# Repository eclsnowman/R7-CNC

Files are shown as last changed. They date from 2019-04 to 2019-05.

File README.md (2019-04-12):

# R7-CNC BY SMW3D AKA Hobby-Fab (w/ Eric Lien)
=========

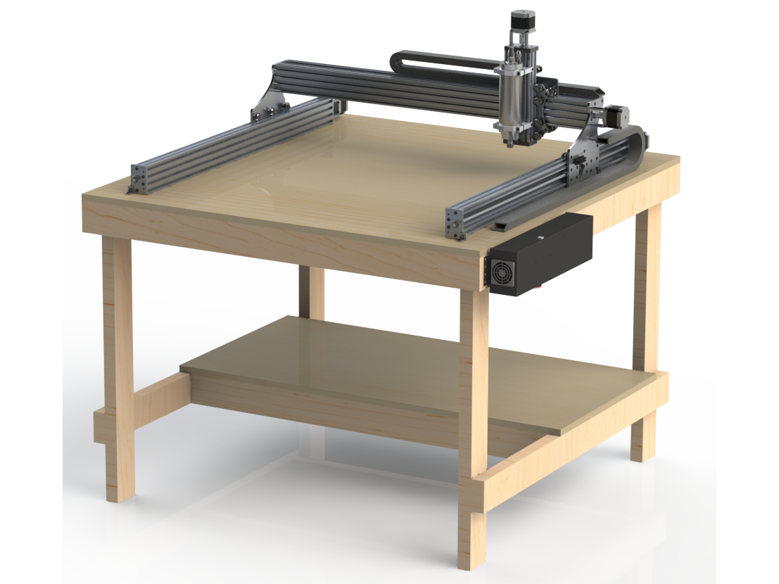
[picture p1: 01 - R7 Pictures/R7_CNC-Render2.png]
R7-CNC Render Image2


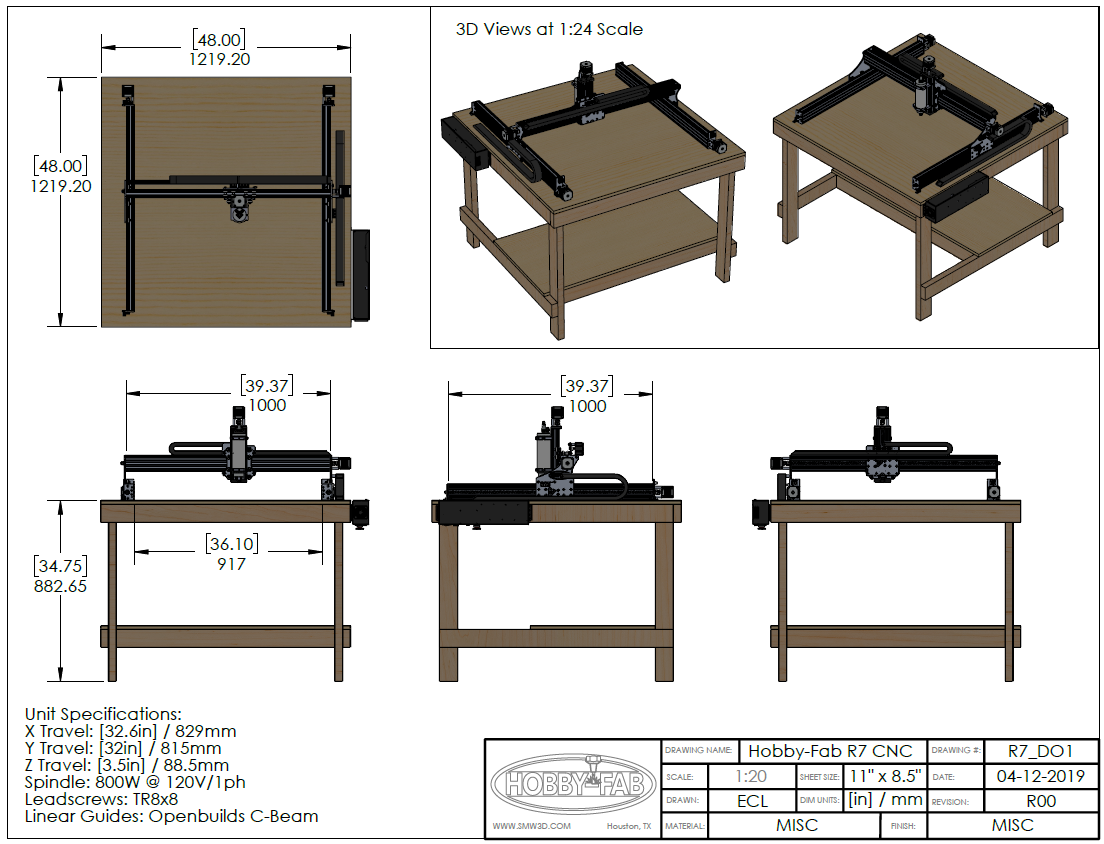
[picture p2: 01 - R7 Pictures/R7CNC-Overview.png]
R7-CNC Overview


The R7-CNC is a strong and capable router style CNC that was sold by SMW3D which later changed its name to Hobby-Fab. I have had the pleasure of knowing Brandon Satterfield for many years through the now defunct Google+. Over those years I have had the pleasure of working on many cool project with Brandon and the team at SMW3D. The R7 CNC was one of those projects. 

Unfortunately the Chinese market spurring the race to the bottom on maker parts, kits, and components drove Brandon and his team on to greener pastures via the closure of Hobbyfab in 2019. But I am delighted to announce that Brandon has given me the OK to release the designs and plans on many of the cool machines we developed together out here on Github. After the initial designs we worked on together several years ago, Brandon and his team made many improvements and upgrades to those initial designs. There is no better example of that than the R7-CNC which was subject to continuous improvement. The files here are my best attempt to cleanup and document via detailed 3D models the final product as shipped by Hobbyfab.

In this Github you will find a detailed 3D model generated by me for the mechanical setup of the machine. I have the files saved in several formats. I work in solidworks natively, but I have exported the model into Fusion360, X_T, Step, 3D-PDF. In addition I have generated a DXF for the plates that make up the major fabricated components.

In addition to the models, I have included several of the supporting files Brandon had developed for his product, like manuals, reference material, etc. Some of this material might be slightly outdated to the model. But it should aid in helping a perspective maker in replicating this capable CNC router design on their own.

I would like to end this by saying Brandon and his group over the years they were in business did amazing work for the community. They sponsored projects to many makers via at cost or free components to develop cool projects. They were always available to answer questions to potential makers on the kits and projects they sold (day or night). The maker community lost something special with the closure of SMW3D/Hobby-Fab. But the impact they left on the maker community will live on.

Thank you Brandon and team. You are amazing. And I am glad to have been but a small part in your chapter of the Maker Revolution story.

-Eric Lien

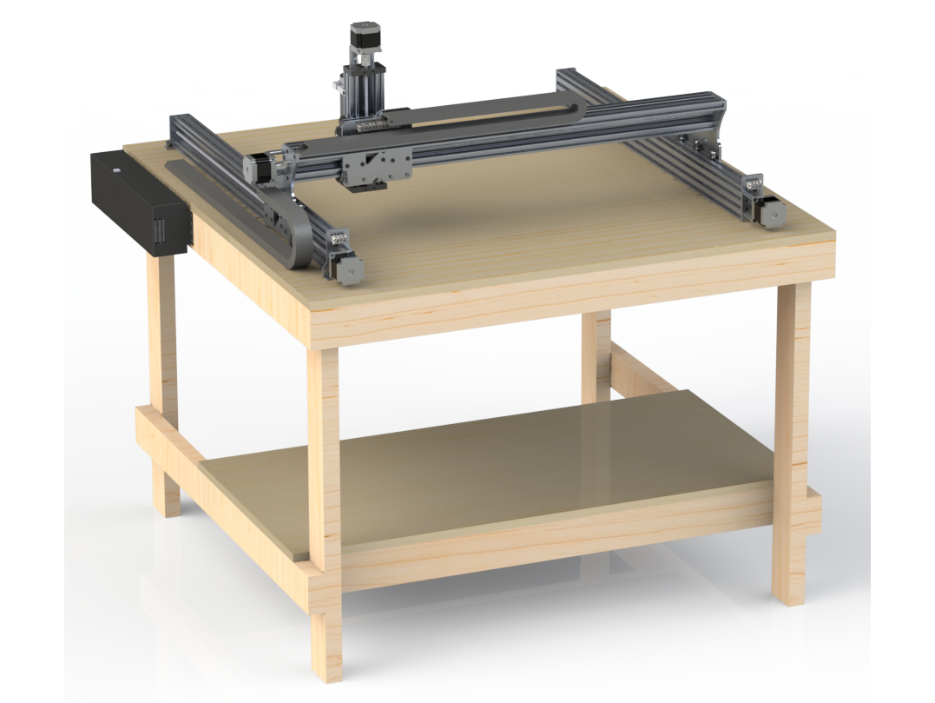
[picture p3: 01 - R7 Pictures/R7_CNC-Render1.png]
R7-CNC Render Image1


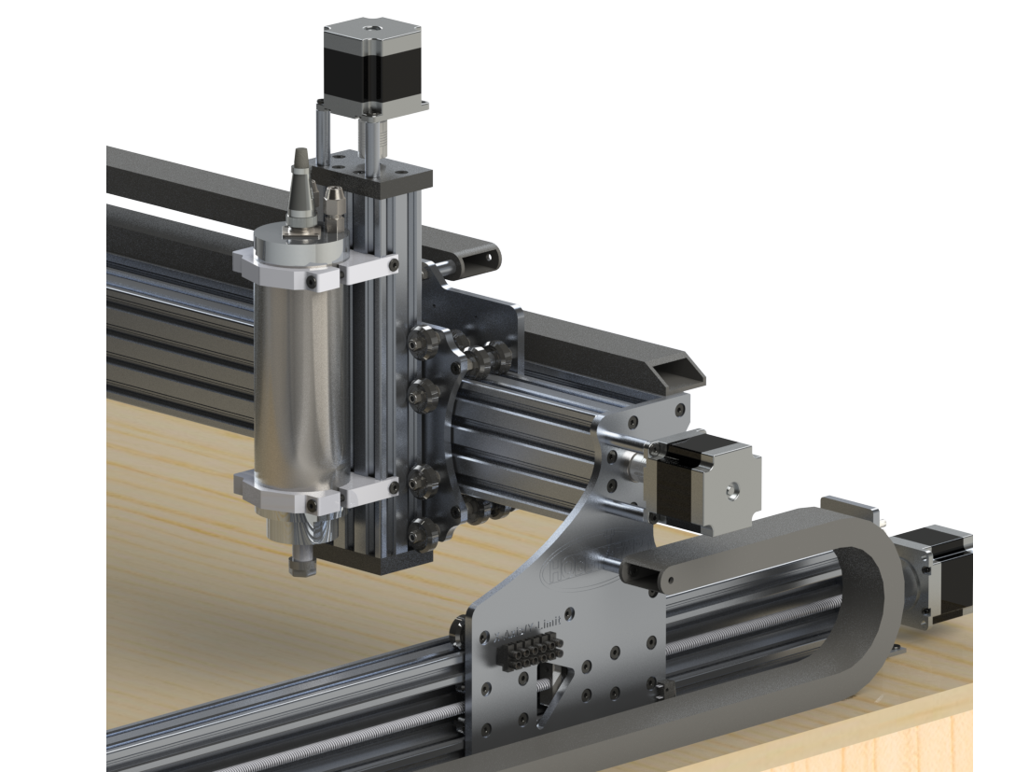
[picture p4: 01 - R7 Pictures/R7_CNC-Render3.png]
R7-CNC Render Image3


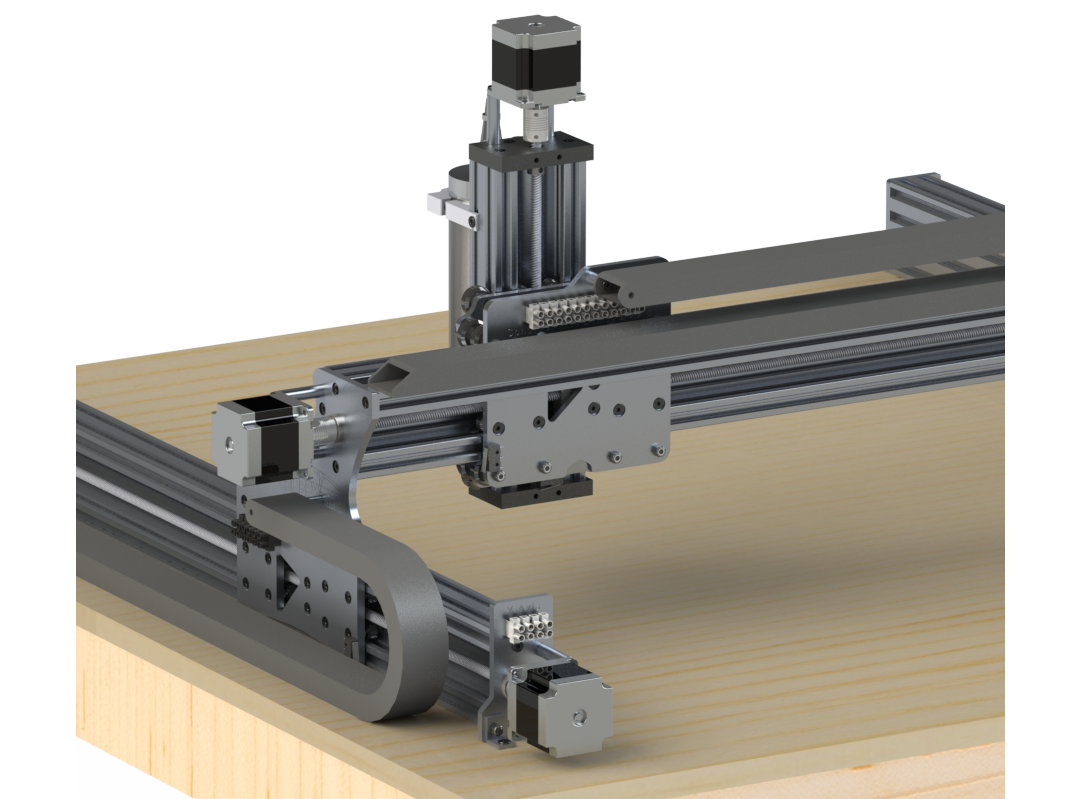
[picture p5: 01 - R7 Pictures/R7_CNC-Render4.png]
R7-CNC Render Image4


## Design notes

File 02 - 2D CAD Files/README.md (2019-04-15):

# Image of DXF 2D Print
=========

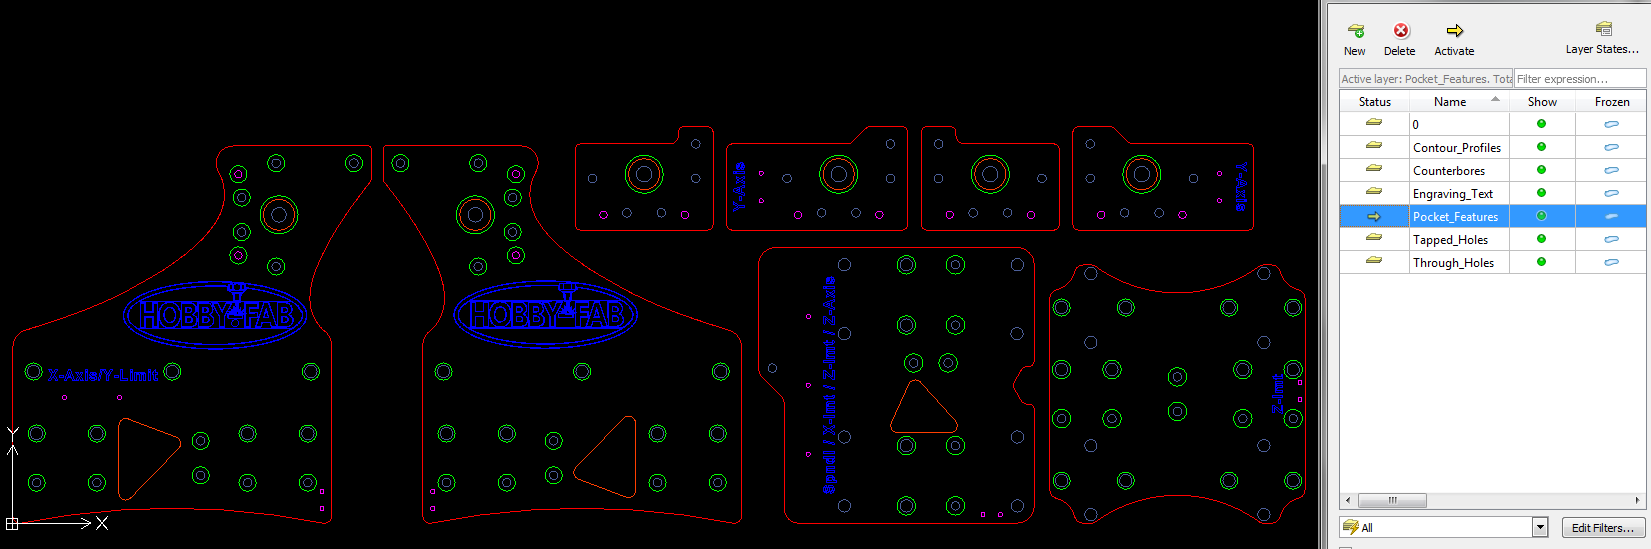
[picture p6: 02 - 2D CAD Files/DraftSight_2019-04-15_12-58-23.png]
Image of DXF


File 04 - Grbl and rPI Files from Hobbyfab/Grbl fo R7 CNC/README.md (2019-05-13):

Grbl files for Hobbyfab R7 CNC, Files based on Spindle Size (example 800W)

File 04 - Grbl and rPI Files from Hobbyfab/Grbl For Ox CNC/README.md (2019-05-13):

Grbl files for Hobbyfab Ox, Files based on Spindle Size (400W vs 600W)

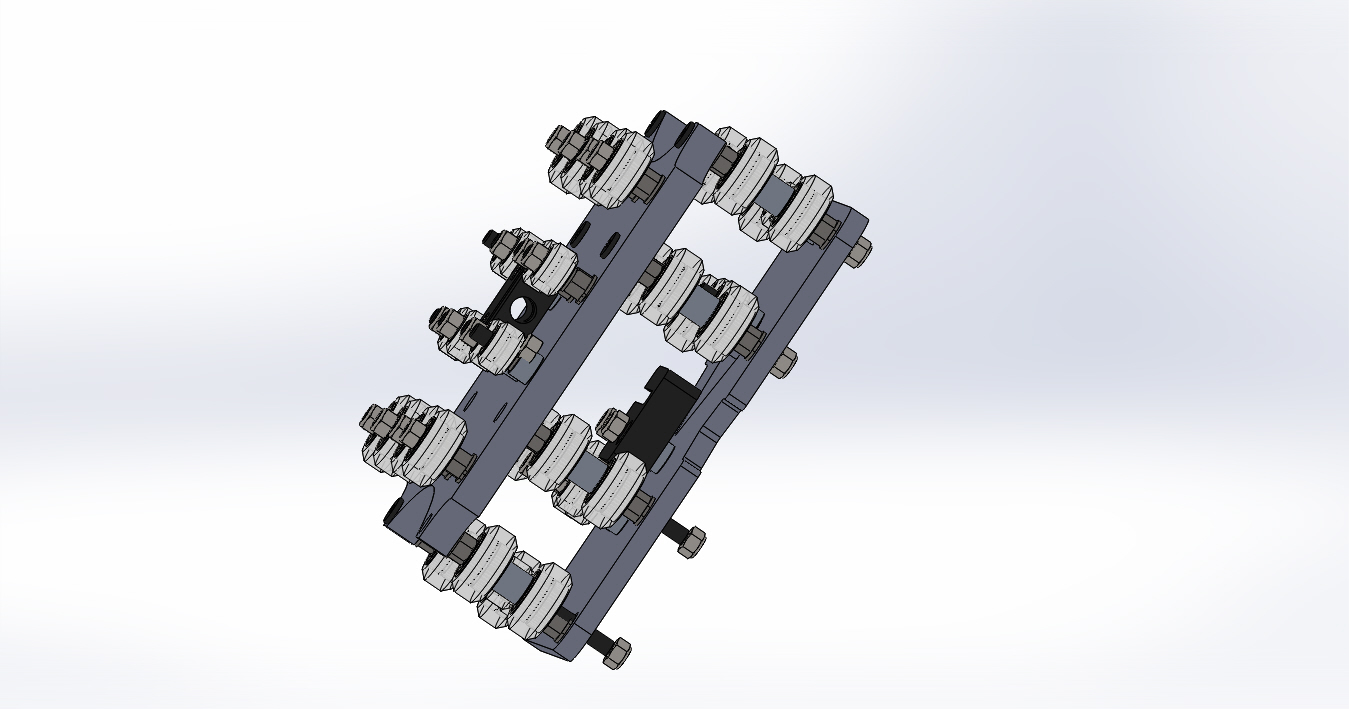
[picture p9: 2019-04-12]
00 - R7 Documentation/Images/X_Z gantry2.JPG

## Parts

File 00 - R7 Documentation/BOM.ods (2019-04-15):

STEP 1 | Qty. | Cost Per Unit | Price
Y Gantry Plate LH | 1
Y Gantry Plate RH | 1
Xtreme Wheels | 6 | $6.75 | $40.50
Mini Xtreme Wheels | 16 | $5.95 | $95.20
Anti-BackLash Acme block | 2 | $9.85 | $19.70
6mm Spacers | 8 | $0.20 | $1.60
6mm Mini Eccentric Spacers | 14 | $2.00 | $28.00
3mm Spacers | 4 | $0.20 | $0.80
M5x20 | 4 | $0.19 | $0.76
M5x25 | 22 | $0.20 | $4.40
 |  | Total | $190.96
STEP 2 | Qty. | Cost Per Unit | Price
Front XZ Gantry Plate | 1 |  | 0
Xtreme Wheels | 8 | $6.75 | $54.00
Mini Xtreme Wheels | 8 | $5.95 | $47.60
Acme Blocks | 2 | $9.85 | $19.70
6mm Spacers | 4 | $0.20 | $0.80
6mm Mini Eccentric Spacers | 12 | $2 | $24
3mm Spacers | 4 | $0.20 | $0.80
M5x20 | 4 | $0.19 | $0.76
M5x25 | 16 | $0.20 | $3.20
250mm ACME | 1 | $9.99 | $9.99
M5 Nuts | 4 | 0.12 | 0.48
 |  | Total | $161.33
STEP 3 | Qty. | Cost Per Unit | Price
Rear XZ Gantry Plate | 1 |  | 0
Anti-BackLash Acme Block | 1 | $9.85 | $9.85
Mini Xtreme Wheels | 8 | $5.95 | $47.60
3mm spacers | 2 | $0.20 | $0.40
m5x20 | 2 | $0.19 | $0.38
m5x25 | 8 | $0.20 | $1.60
6mm Spacers | 4 | $0.20 | $0.80
Eccentric | 4 | $2 | $8
M5 Nuts | 2 | 0.12 | 0.24
 |  | Total | $68.87
STEP 4 | Qty. | Cost Per Unit | Price
Xtreme Wheels | 16 | $6.75 | $108
9mm Spacers | 8 | $0.20 | $2
6mm Mini Eccentric Spacers | 16 | $2.00 | $32
M5x60 | 8 | $0.30 | $2
 |  | Total | $144.00
STEP 5 | Qty. | Cost Per Unit | Price
800w Spindle | 1 | $160 | $160
Spindle Clamps | 2 | 1.25 | $3
Solid black 90s | 8 | $2.25 | $18
M5 T-Nuts | 8 | $0.20 | $2
M5x8 | 8 | $0.18 | $1
M5x10 | 8 | $0.18 | $1
M5x40 | 2 | $0.25 | $1
250mm C-Beam | 1 | 7 | $7
 |  | Total | $192.48
STEP 6 | Qty. | Cost Per Unit | Price
M5x15 | 10 | $0.19 | $1.90
M5x55 | 2 | $0.30 | $0.60
1.5in spacers | 2 | $0.75 | $1.50
608ZZ | 2 | $6.15 | $12.30
lock collar | 1 | $1.20 | $1.20
6.35x8 Coupler | 1 | $1.50 | $1.50
1000mm Acme | 1 | $31.50 | $31.50
1000mm 20x20 | 1 | $10 | $10.00
1000mm C Beam | 1 | $28 | $28.00
NEMA 23 2.8A | 1 | $23.99 | $23.99
 |  | Total | $112.49
Step 7 | Qty. | Cost Per Unit | Price
NEMA 23 2.8A | 2 | $23.99 | $47.98
6.35x8 Coupler | 2 | $1.50 | $3.00
End corner caps | 4 | 10 | $40.00
Lock collar | 2 | $1.20 | $2.40
608ZZ | 4 | $6.15 | $24.60
C-Beam 1000mm | 2 | $28.00 | $56.00
1.5" spacers | 4 | $0.75 | $3.00
M5x55mm bolts | 4 | $0.30 | $1.20
M5x20mm bolts | 20 | $0.19 | $3.80
Single corner bracket | 4 | 1 | $4.00
M5 nuts | 4 | $0.12 | $0.48
1000mm ACME | 2 | $31.50 | $63.00
ACME flange nut | 1 | 6.25 | $6.25
 |  | Total | $255.71
Step 8 | Qty. | Cost Per Unit | Price
C-beam end plates | 2 | $8.75 | $17.50
M5x55 | 2 | $0.30 | $0.60
1.5" spacers | 2 | $0.75 | $1.50
250mm ACME | 1 | $9.99 | $9.99
688zz | 2 | $0.99 | $1.98
6.35mm x 8mm coupler | 1 | $1.50 | $1.50
NEMA 23 2.8A | 1 | $23.99 | $23.99
M5x25mm | 8 | $0.19 | $1.52
Lock Collar | 2 | $1.20 | $2.40
 |  | Total | $60.98
Step 9 | Qty. | Cost Per Unit | Price
3/16" ID 5/16" OD vinyl tubing | 30 | 1.08 | 32.4
4 wire 22g | 30 | $0.50 | $15.00
16-3 wire | 15 | 0.5 | 7.5
15mmx30mm cable chain | 2 | $16.00 | $32.00
M5 drop-in T-nut | 1 | $0.75 | $0.75
M5 x 10mm bolt | 1 | $0.18 | $0.18
small heat shrink tubing | 4 | $1.25 | $5.00
M5x65mm bolt | 1 | $0.30 | $0.30
40mm spacer | 1 | $0.20 | $0.20
9mm spacer | 1 | $0.20 | $0.20
6mm spacer | 2 | $0.20 | $0.40
Water pump | 1 | $25.00 | $25.00
M5x20mm bolt | 1 | $0.19 | $0.19
Large heat shrink tubing | 4 | $1.25 | $5.00
Sheathing 10mm | 10 | $0.99 | $9.90
M5 nut | 1 | $0.12 | $0.12
Power cable | 1 | $6.50 | $6.50
 |  | Total | $140.64
Step 10 | Qty. | Cost Per Unit | Price
Fan | 1 | $4.99 | $4.99
Inverter | 1 | $150 | $150
24V power supply | 1 | $31.99 | $32.99
Power Cable | 1 | $6.50 | $6.50
 |  | Total | $194.48
 |  | Grand Total | $1,521.94

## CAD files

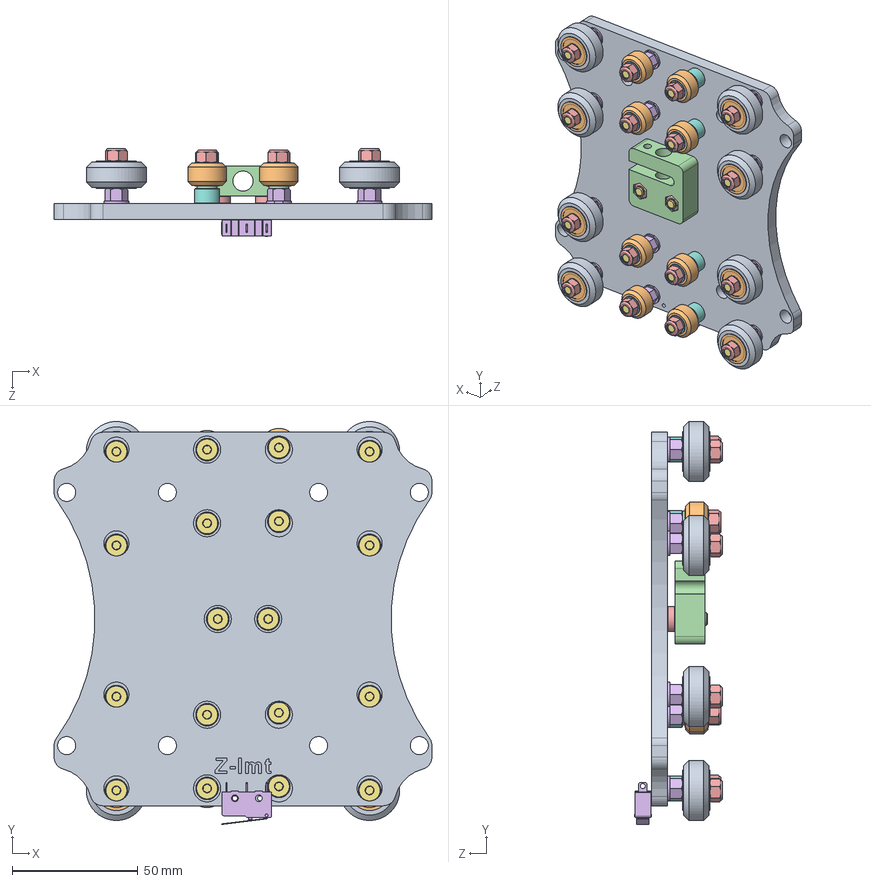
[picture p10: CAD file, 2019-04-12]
03 - 3D CAD Files/00 - Solidworks/01 - Sub Assemblies/Front XZ Gantry Plate.SLDASM
150.0 x 160.0 x 35.1 mm
R7-CNC_Plates
Xtreme Mini V Wheel x 8
Ball Bearing 5 x 10 x 4.2 x 16
Precision Shim 8 x 5 x 1 x 16
Nylon Insert Lock Nut M5 x 18
Mini Eccentric Spacer 6mm x 12
Low Profile Screw M5 x 18
Aluminum Spacer 6mm x 4
Xtreme Solid V Wheel x 8
Ball Bearing 5 x 16 x 5 x 16
Precision Shim 10 x 5 x 1 x 8
8mm Acme Anti Backlash Nut Block
Aluminum Spacer 3mm x 2
Micro Switch Button

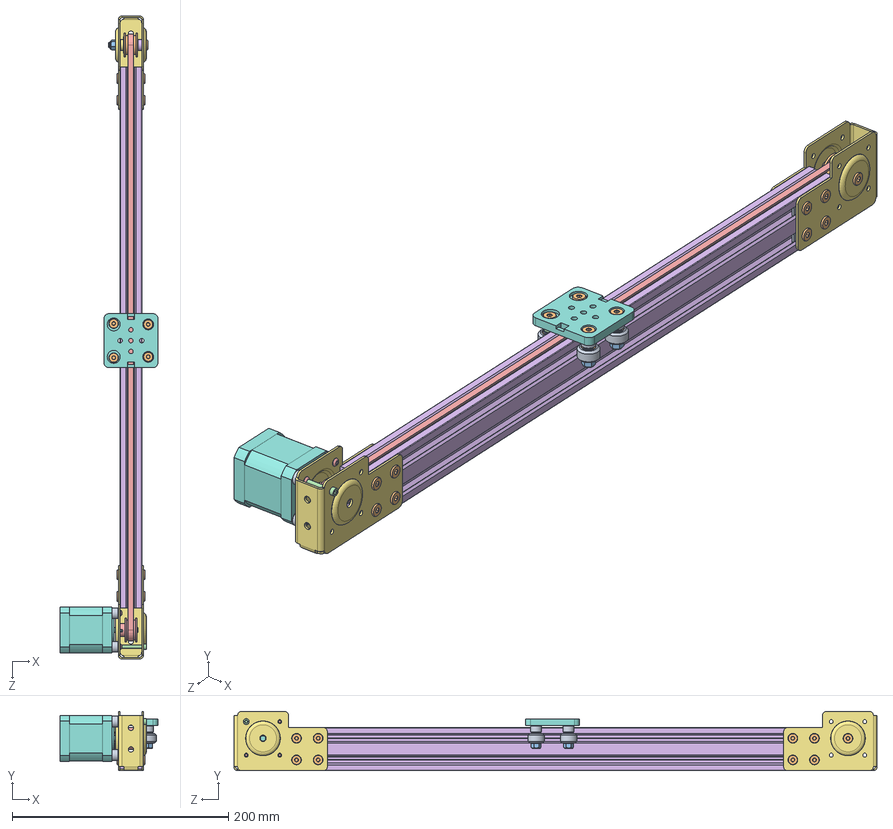
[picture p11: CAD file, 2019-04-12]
03 - 3D CAD Files/00 - Solidworks/ZZ - Openbuilds Library/Assemblies/Mini V Linear Actuator/Mini V Linear Actuator 500mm.SLDASM
90.6 x 54.9 x 594.7 mm
Double Tee Nut x 8
Low Profile Screw M5 x 21
Nylon Insert Lock Nut M5 x 5
Button Head Socket Cap Screw M3 x 4
V-Slot 20x40x500 Linear Rail
Linear Actuator End Mount x 2
Nema 17 Stepper Motor
Aluminum Spacer 6mm x 6
Smooth Idler Pulley Wheel
Ball Bearing 5 x 16 x 5 x 2
Nylon Spacer 0.125in
GT2 Timing Pulley 30 Tooth
Aluminum Spacer .25in
Aluminum Spacer .125in
Mini V Wheel Plate
Delrin Mini V Wheel x 4
Ball Bearing 5 x 10 x 4.2 x 8
Precision Shim 8 x 5 x 1 x 8
Mini Eccentric Spacer 6mm x 2
GT2 Belt 1140mm

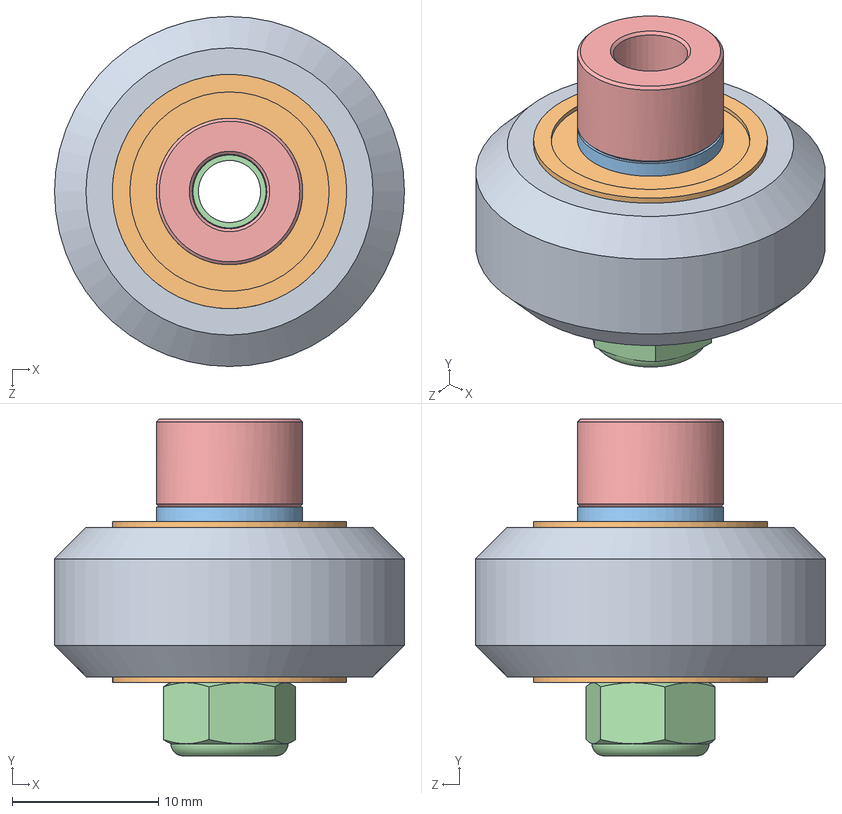
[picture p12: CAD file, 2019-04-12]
03 - 3D CAD Files/00 - Solidworks/ZZ - Openbuilds Library/Assemblies/Wheels/Solid V Wheel.SLDASM
23.9 x 23.0 x 23.9 mm
Solid V Wheel
Ball Bearing 5 x 16 x 5 x 2
Precision Shim 10 x 5 x 1 x 2
Nylon Insert Lock Nut M5
Aluminum Spacer 6mm

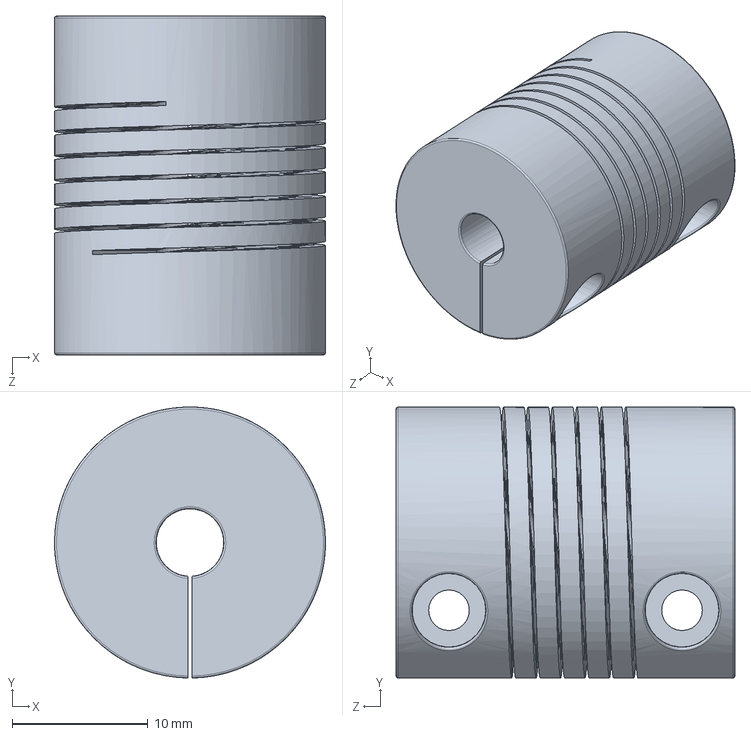
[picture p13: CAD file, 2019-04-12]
03 - 3D CAD Files/00 - Solidworks/01 - Sub Assemblies/Nema23 Drive/8mm x 6.35mm Flexible Coupling.SLDASM
20.0 x 20.0 x 25.0 mm

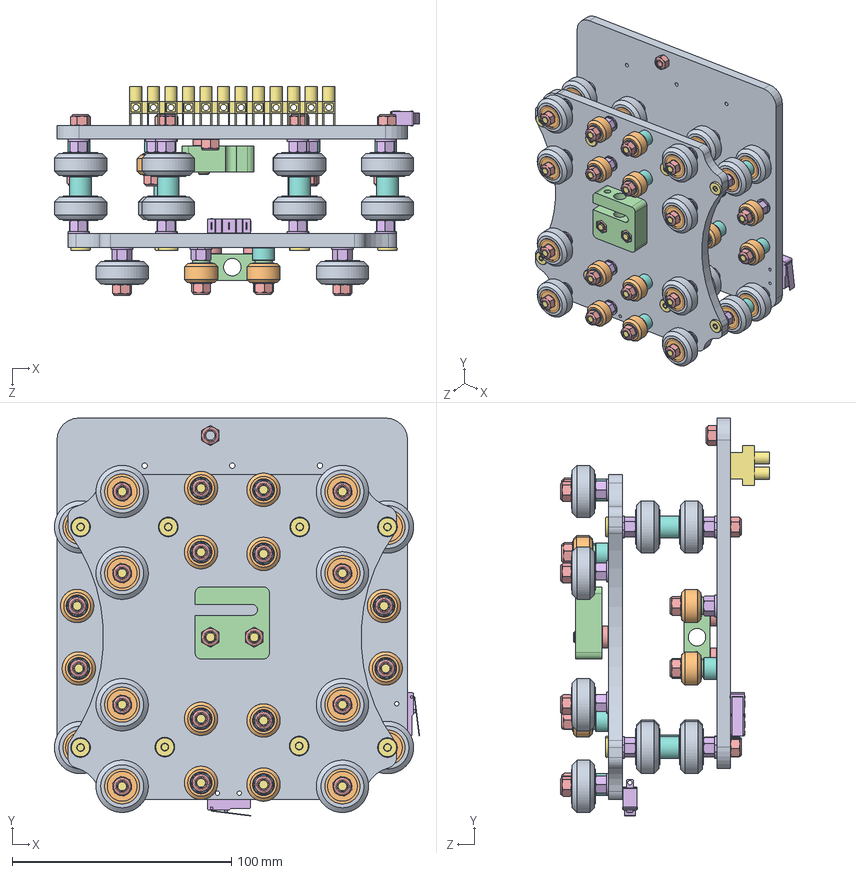
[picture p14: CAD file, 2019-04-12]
03 - 3D CAD Files/00 - Solidworks/01 - Sub Assemblies/XZ_Full_Carriage.SLDASM
166.6 x 181.6 x 95.5 mm
R7-CNC_Plates x 2
Xtreme Mini V Wheel x 16
Ball Bearing 5 x 10 x 4.2 x 32
Precision Shim 8 x 5 x 1 x 32
Nylon Insert Lock Nut M5 x 37
Mini Eccentric Spacer 6mm x 32
Low Profile Screw M5 x 36
Aluminum Spacer 6mm x 8
Xtreme Solid V Wheel x 24
Ball Bearing 5 x 16 x 5 x 48
Precision Shim 10 x 5 x 1 x 24
8mm Acme Anti Backlash Nut Block x 2
Aluminum Spacer 3mm x 4
Micro Switch Button x 2
7618K618_TOUCH-SAFE TERMINAL BLOCK
Aluminum Spacer 9mm x 8

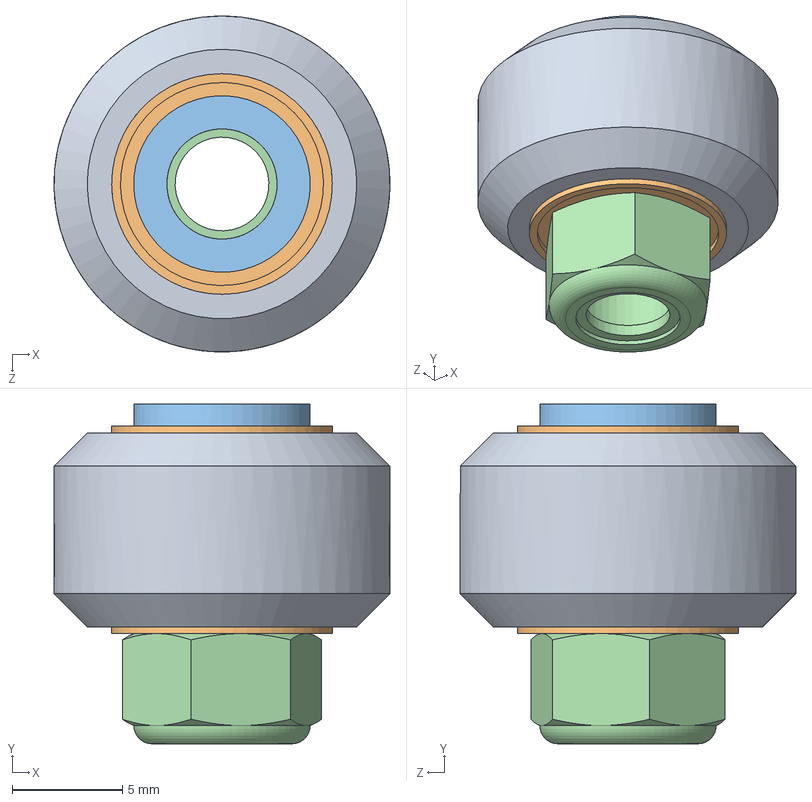
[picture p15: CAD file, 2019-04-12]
03 - 3D CAD Files/00 - Solidworks/ZZ - Openbuilds Library/Assemblies/Wheels/Xtreme Mini V Wheel.SLDASM
15.2 x 15.4 x 15.2 mm
Xtreme Mini V Wheel
Ball Bearing 5 x 10 x 4.2 x 2
Precision Shim 8 x 5 x 1 x 2
Nylon Insert Lock Nut M5

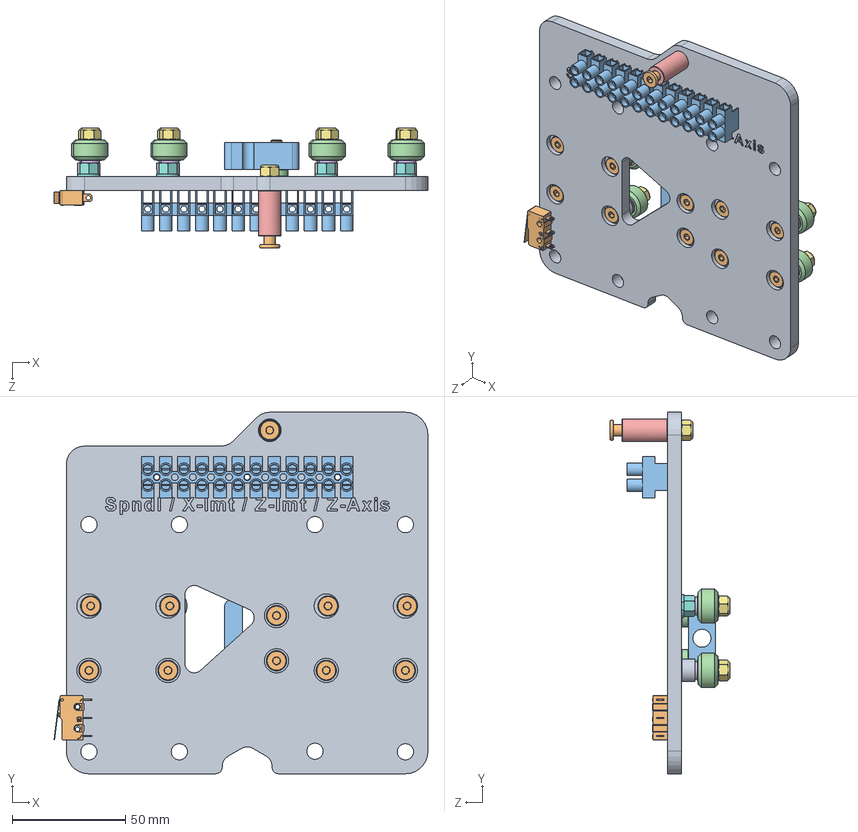
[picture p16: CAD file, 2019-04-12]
03 - 3D CAD Files/00 - Solidworks/01 - Sub Assemblies/Rear XZ Gantry Plate.SLDASM
165.5 x 160.0 x 53.1 mm
R7-CNC_Plates
Micro Switch Button
7618K618_TOUCH-SAFE TERMINAL BLOCK
Xtreme Mini V Wheel x 8
Ball Bearing 5 x 10 x 4.2 x 16
Precision Shim 8 x 5 x 1 x 16
Nylon Insert Lock Nut M5 x 11
Mini Eccentric Spacer 6mm x 4
Aluminum Spacer 6mm x 4
Low Profile Screw M5 x 11
8mm Acme Anti Backlash Nut Block
Aluminum Spacer 3mm x 2
Aluminum Spacer 20mm

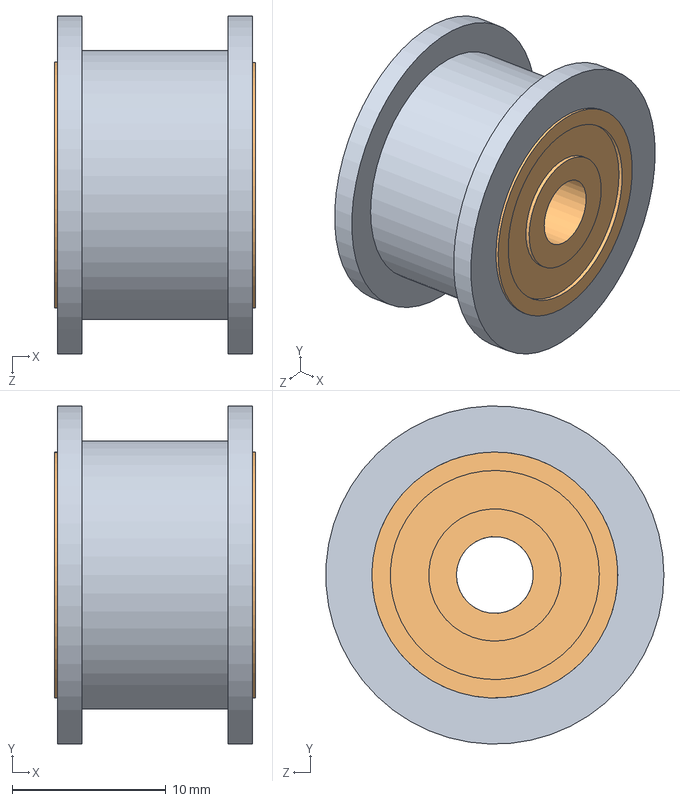
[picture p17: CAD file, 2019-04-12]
03 - 3D CAD Files/00 - Solidworks/ZZ - Openbuilds Library/Assemblies/Wheels/Smooth Idler.SLDASM
13.1 x 22.0 x 22.0 mm
Smooth Idler Pulley Wheel
Ball Bearing 5 x 16 x 5 x 2
Nylon Spacer 0.125in

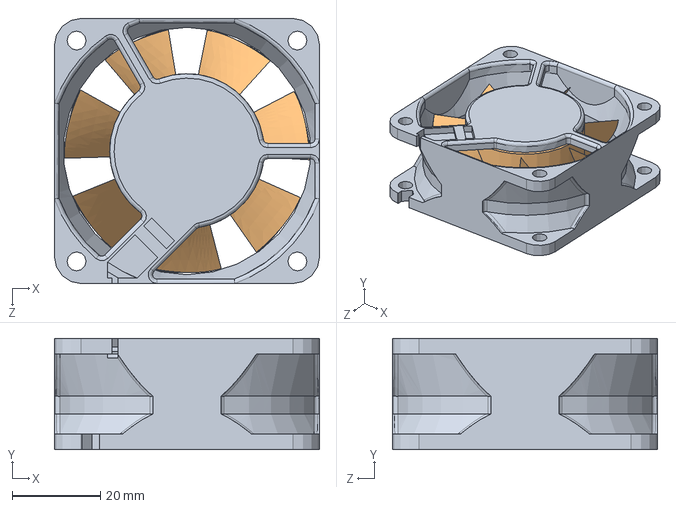
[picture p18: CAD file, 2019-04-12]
03 - 3D CAD Files/00 - Solidworks/01 - Sub Assemblies/Control Box (All IN ONE)/Ventola_50x50.SLDASM
60.0 x 25.2 x 60.0 mm
ventola_1
ventola_2

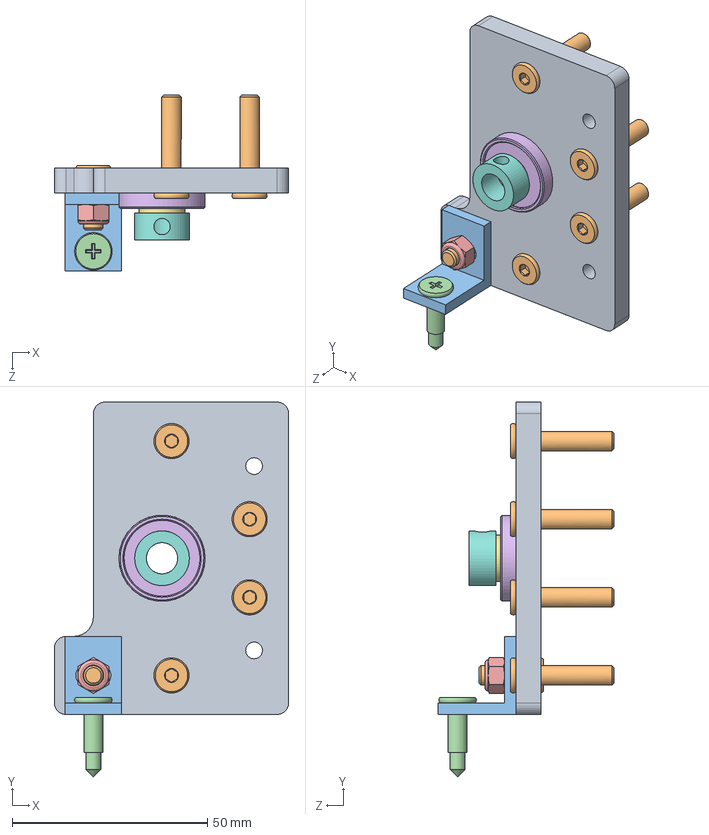
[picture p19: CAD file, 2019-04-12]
03 - 3D CAD Files/00 - Solidworks/01 - Sub Assemblies/Front_Left_Y-Axis_Corner.SLDASM
60.0 x 96.0 x 45.0 mm
R7-CNC_Plates
Low Profile Screw M5 x 5
L Bracket Single
Self Tapping Screw
Nylon Insert Lock Nut M5
608ZZ_Bearing
Shim Washer 8mm
Lock Collar 8mm

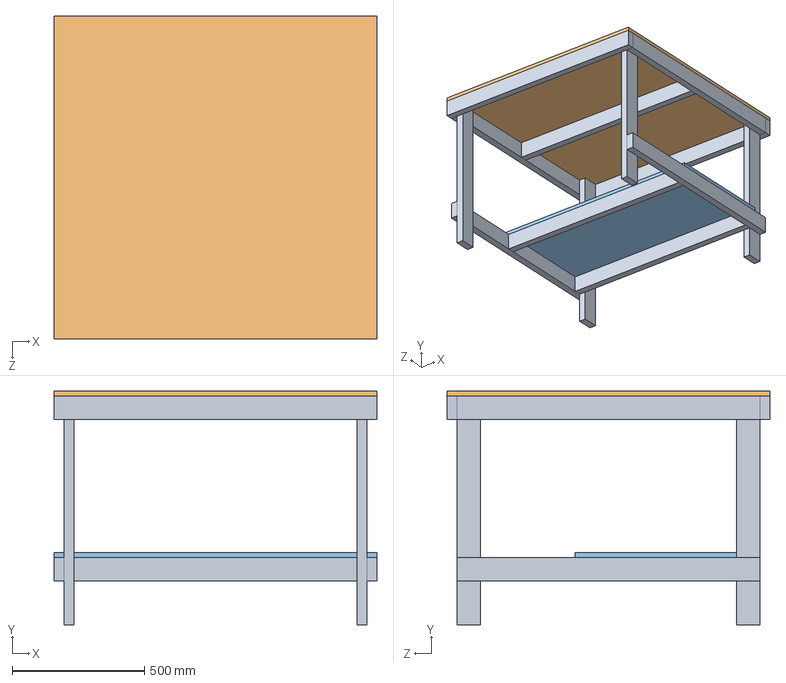
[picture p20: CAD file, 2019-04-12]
03 - 3D CAD Files/00 - Solidworks/01 - Sub Assemblies/Wood Base/Workbech.SLDASM
1219.2 x 882.7 x 1219.2 mm
2x4_Frame
Workbench_Top
Workbench Lower Shelf

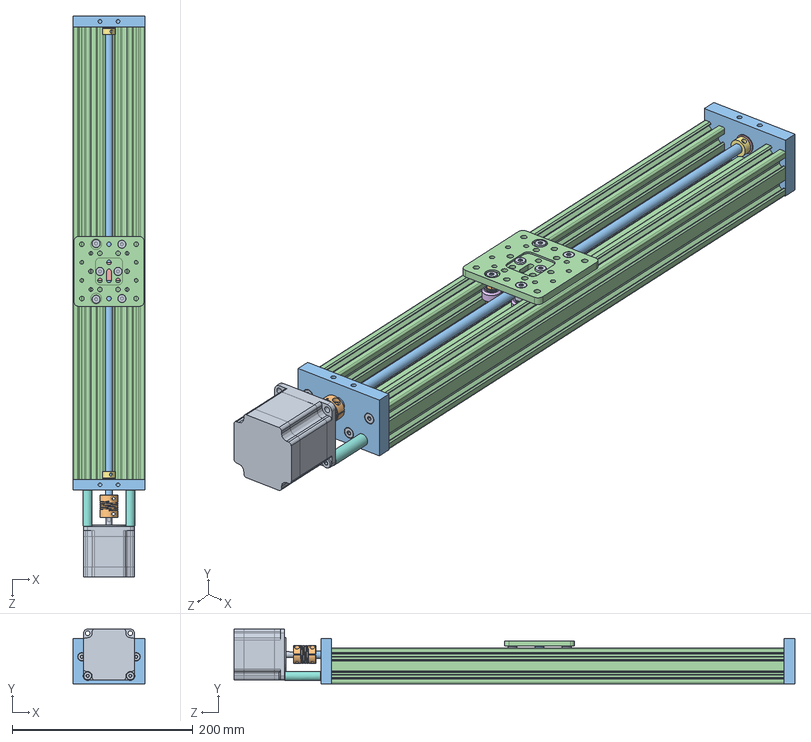
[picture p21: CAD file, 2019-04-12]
03 - 3D CAD Files/00 - Solidworks/ZZ - Openbuilds Library/Assemblies/C-Beam Linear Actuator/C-Beam Linear Actuator 500mm.SLDASM
80.0 x 60.7 x 620.0 mm
Low Profile Screw M5 x 16
Nylon Insert Lock Nut M5 x 6
C-Beam End Mount x 2
C-Beam 40x80x500 Linear Rail
Ball Bearing 8 x 16 x 5 x 2
Shim Washer 8mm x 2
Lock Collar 8mm x 2
Aluminum Spacer 40mm x 2
Nema 23 Stepper Motor
Flexible Coupling 0.25in x 8mm
8mm leadscrew 540mm
C-Beam Gantry Plate
8mm Acme Nut Block
Xtreme Mini V Wheel x 4
Ball Bearing 5 x 10 x 4.2 x 8
Precision Shim 8 x 5 x 1 x 8
Aluminum Spacer 6mm x 2
Mini Eccentric Spacer 6mm x 2
Aluminum Spacer 3mm x 2

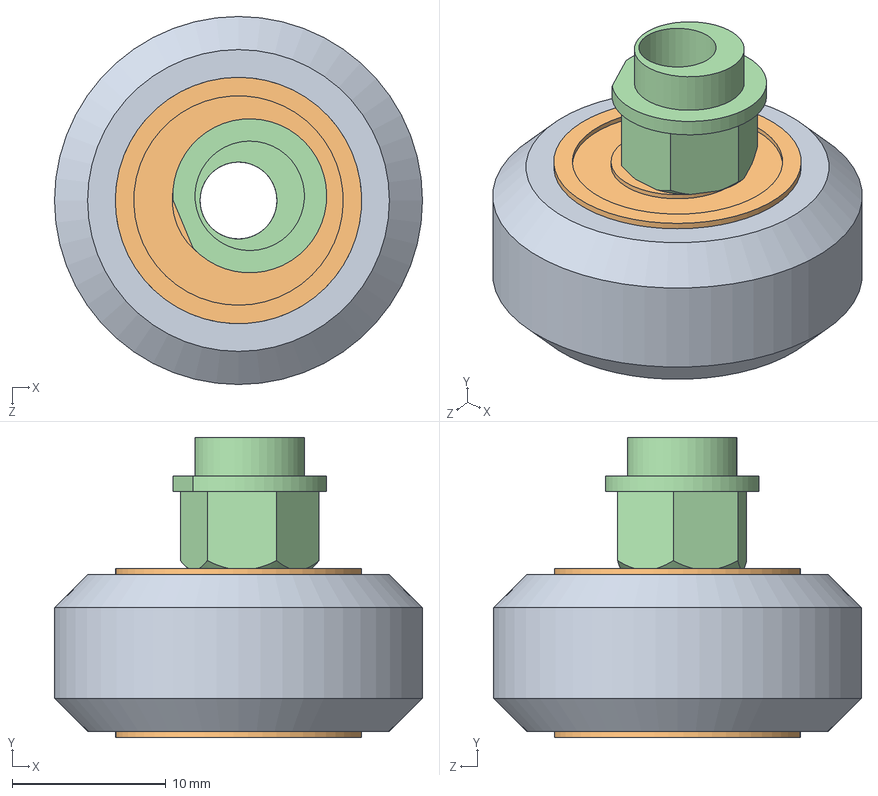
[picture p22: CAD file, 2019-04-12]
03 - 3D CAD Files/00 - Solidworks/ZZ - Openbuilds Library/Assemblies/Wheels/Xtreme V Wheel.SLDASM
23.9 x 19.5 x 23.9 mm
Xtreme Solid V Wheel
Ball Bearing 5 x 16 x 5 x 2
Precision Shim 10 x 5 x 1
Mini Eccentric Spacer 6mm

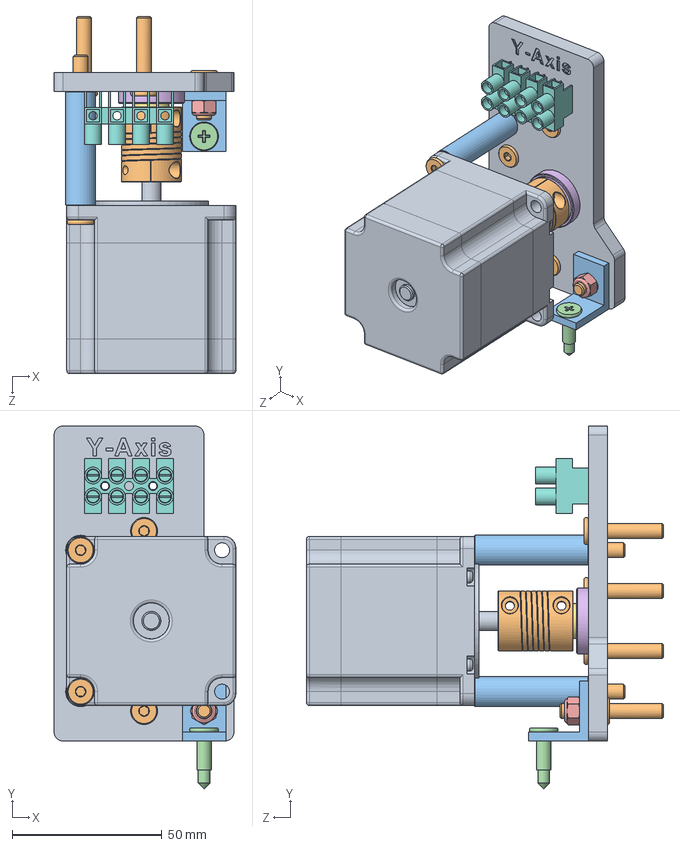
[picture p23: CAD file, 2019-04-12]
03 - 3D CAD Files/00 - Solidworks/01 - Sub Assemblies/Left_Driven_Y-Axis_Corner.SLDASM
60.6 x 121.0 x 119.1 mm
R7-CNC_Plates
Low Profile Screw M5 x 7
L Bracket Single
Self Tapping Screw
Nylon Insert Lock Nut M5
608ZZ_Bearing
Shim Washer 8mm
7618K613_TOUCH-SAFE TERMINAL BLOCK
Nema23_56mm_6.35mmShaft_13Nm
8mm x 6.35mm Flexible Coupling
Aluminum Spacer 1.5in x 2

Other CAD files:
03 - 3D CAD Files/00 - Solidworks/ZZ - Openbuilds Library/Assemblies/C-Beam Linear Actuator/C-Beam Linear Actuator 250mm.SLDASM
03 - 3D CAD Files/00 - Solidworks/ZZ - Openbuilds Library/Assemblies/Wheels/Delrin Mini V Wheel.SLDASM
03 - 3D CAD Files/00 - Solidworks/01 - Sub Assemblies/Nema23 Drive/Nema_23Drive_Module.SLDASM
03 - 3D CAD Files/00 - Solidworks/01 - Sub Assemblies/Right_Driven_Y-Axis_Corner.SLDASM
00 - R7 Documentation/DXF/20x40 slider housing.DXF
00 - R7 Documentation/DXF/20x40 slider.DXF
00 - R7 Documentation/DXF/65 mm clamp R3 inches.SLDPRT.DXF
00 - R7 Documentation/DXF/Dewalt 611 clamp.DXF
02 - 2D CAD Files/R7-CNC_Plates.DXF
03 - 3D CAD Files/00 - Solidworks/01 - Sub Assemblies/Control Box (All IN ONE)/110 AC inlet.SLDPRT
03 - 3D CAD Files/00 - Solidworks/01 - Sub Assemblies/Control Box (All IN ONE)/Amazon_Electrical_Fused_Plug.SLDPRT
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

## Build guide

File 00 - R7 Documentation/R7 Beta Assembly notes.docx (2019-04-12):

Some of these notes may be trivial, but felt it was necessary to mention since it is beta.

Needed tools for day-to-day use and assembly:

Collet Wrench

USB Cable

Thread Lock

8mm Combination Wrench

Red Thread Loctite

4mm Allen Wrench

3 mm Allen Wrench

2.5 mm Allen Wrench

Metal File

Combo Square or Steel Square

Assembly Notes, Step 1:

-Smooth/file down sharp edges/burs on aluminum gantry plate holes and edges. Could possibly interfere with screws/eccentric spacers from setting flush or lead to cuts from sharp edges.

-ACME Block, may want to mention the M5 20mm length screw (20 vs 25) as you are building it (was mentioned initially in the parts lay out, but not in the assembly)

-Add 3rd screw to the ACME block? With just two screw, has some alignment play in it and worried about the long thread rod alignment/assembly later.

-Cherry pick the nylon nuts for the inner mini extreme wheels, otherwise will have to file them down later. Can visually see which nylon nuts have too much nylon washer sticking out into the screw space and will flare out once the screw is tightened.

-Maybe mention something about how much to screw/tighten the adjustment Allen screw on the ACME Blocks, before assembly to the gantry plate

-Assembling the normal extreme wheels to the plate(s), the shim between the bearings will slide around some. When trying to align the screw through the bearings and shim, just spin the wheel on the screw and it will typically align and screw will go through.

-I took a marker, and made a tic mark at the same location on the outer edge of all eccentric spacers (thinnest section), for referencing/adjusting them during assembly. Also, make sure you turn/adjust all eccentric spacers in the same direction (CW vs CCW) during adjustments and keep your orientation the same all the way through, while referencing from the same side of plate.

-After tightening each Extreme wheels, check to make sure they will roll/spin freely with no binding as they turn, before proceeding further.

-Update build/assembly video of the extreme wheels not using the shim (.2mm spacer) during the assembly, even though it was noted at the beginning of the video that it was removed from the BOM.

Assembly Notes, Step 2:

-Concern with tightening the two ACME Blocks down enough to the Gantry Plate, but loose enough not to bind the Threaded Rod. Currently, cannot get the blocks tight enough so there is no loose play in them w/o the rod threaded through them and still have the threaded rod turn with ease once it is in place.

- Triple check that mini extreme wheels are adjusted correctly. If not, incorrect adjustments will be more pronounced when adjusting the outside extreme wheels.

Assembly Notes, Step 4:

The tick mark (suggested earlier) on the outside of the eccentric spacers, will come in handy during this part of the assembly. Line up the tick marks on the eccentric nuts as you thread the 60mm screw through, so you are not fighting against the wheels pushing against the C-Beam.

Tip for lining up the 2nd eccentric nut with the 2nd extreme wheel; Use one of the screws or allen wrench and slide it in from the nylon nut side of the plate to hold the 2nd eccentric spacer in place. Slide the 2nd extreme wheel in and twist (will help line up the washer/spacer in the extreme wheel) the 60mm screw though 2nd extreme wheel and line it up with the 2nd eccentric nut, then just push out the screw or allen wrench holding the 2nd eccentric nut in place.

Idea for an Adjustable Tension Anti-Backlash Nut/Block

-Run M5 screws through springs, may need to add small washer(s) too each end of the springs as well.

-Then through the 8mm ACME Nut Plate outside holes (non-threaded)

-Then screws the M5’s into a threaded ACME Block on the opposite side.

(or place spring between the Nut Plate and the block)

Tightening or loosening the spring loaded screws will add or remove tension to the ACME Threaded Rod, as it runs through both Nut Plate and Block. This could work on the Z-Axis plate, would be able to access the screws heads from behind the edges of the plate, and inside the C-Beam (could add a hole/window to see the screw heads). Of course, accessing the screws around mini wheel post, may require the nut plate/block size to be adjusted with the current screw hole placement.

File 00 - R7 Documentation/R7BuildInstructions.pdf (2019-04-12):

Last updated: 08/13/20108 Rev. 9

1

# R7 Build Instructions

## 1. INTRODUCTION

The R7 is so named as this was the revision the SMW3D/ Hobby-Fab team released; this DIY CNC router kit. The kit is fully open source. In addition, the kit was released in beta and all feedback taken to improve build and functionality. Thank you for joining us on this journey. We truly hope this build will help makers to achieve the satisfaction of creating a machine that will provide years of creativity with their own two hands.

## 2. SET-UP

We would love for you to rip open this package like it’s Christmas morning and you are eight years old again. We must warn though, we have individually bagged the steps and they will match the below inventory as well as the videos on YouTube on the SMW3D/Hobby-Fab page. The videos are labeled R7v1, this means R7 video one, etc. Please DO NOT open every bag and dump the build on the table. This will severely impact your build time and locating the proper parts for the steps. The build videos are very outdated, they should only be used for reference.

We also advise finding a large, clean, flat surface to build your kit. The first few steps can certainly be performed on a smaller surface however, as the build grows, you will need a four foot by four-foot area flat surface. It is also advised that you lay out each step individually with all parts for the respective step. Lastly, before starting the build, please note the BOM (Bill of Materials) is described below and two columns are present after the item description. Please open each bag prior to build and count each item and check it off the below list. If anything is missing, please contact us at contact@Hobby-Fab.com. Performing this task now will prevent having to put off your build in the event we missed something.

Finally, please have fun and take your time. The build process will control all your cuts after, build it once and build it right. The machine will provide years of great service.

Tools Required: (all should be locally available) Additional Items Required

Metric allen wrench set | Bucket for water
Soldering iron and solder | Table
Metric tap set | Computer
8mm combination wrench | USB A to B cable
10mm combination wrench | Square and level

Last updated: 08/13/20108 Rev. 9

2

Hand file

## 3. Build and BOM

The steps shown here will correspond with the SMW3D build videos. It should be noted these videos are quickly getting outdated due to amazing feedback from users.

NOTE: as of November 2017, the mini wheels running inside the beam may be changed to Delrin.

NOTE: as of November 2017, mechanical limits are included in all R7 kits. The limits get installed as such:

Y gantry plate – limit faces rear of machine

X gantry plate – limit faces the right-hand side of the build looking at the machine

Z gantry plate – limit faces down

All wired NO

Step One:

In the first step, you will be assembling the Y gantry plates. These plates will run on the side of the R7 as you are facing the machine. One notable change from the videos is the .2mm shims are no longer needed. At the end of this step you will have two assembled Y gantry plates, each with eight mini wheels and three large wheels (all on M5 x25 bolts), the ACME block will also be installed (M5 x 20 bolts). Take your time on the wheels. If all wheels touch the C-Beam, you are in a great spot. We state in the video a tension is required. We have found this is not true. Each plate can take up to an hour and a half to completely assemble. So, sit back, relax, and let's build.

Last updated: 08/13/20108 Rev. 9

3

STEP 1 | Qty. | Smw3D | Builder
Y Gantry Plate LH | 1
Y Gantry Plate RH | 1
Large Xtreme Wheels | 6
Mini Delrin Wheels | 16
Adjustable Tension Anti-Backlash Nut | 2
6mm Spacers | 8
6mm Mini Eccentric Spacers | 14
3mm Spacers | 4
M5x20 Bolt | 4
M5x25 Bolt | 22

Last updated: 08/13/20108 Rev. 9

4

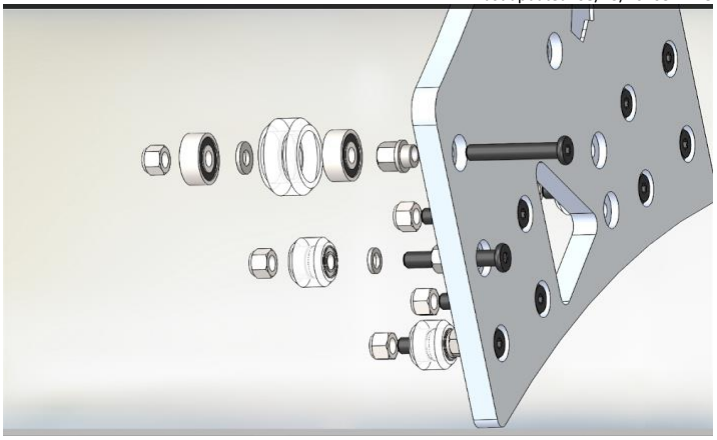
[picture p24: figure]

Note, the large wheels get a shim from the wheel bag between the bearings but not between the eccentric spacer and bearing. The mini wheels get a shim from the wheel kit, between the bearings in the wheel and between the bearing and eccentric spacer. All bolts are M5x25mm bolts. Note, you will most likely need to remove the limit switch to install the one wheel bolt that resides behind it.

Begin by installing the standard spacers on the smaller holes (bottom row), these will be a reference for the rest of the wheels. Tighten these with a small amount of torque, do not tighten so much that the wheel drags or locks. Next, install the next row up eccentric spacers and mini-wheels. Before tightening, turn the eccentrics until the wheel on this bolt is as close to the reference wheel below it. Install and correctly tension the inner mini-wheels on the inside of the C-Beam (250 length), before installing the outer larger wheels. Install the large wheels on the eccentrics and adjust to the beam in the same fashion.

Last updated: 08/13/20108 Rev. 9

5

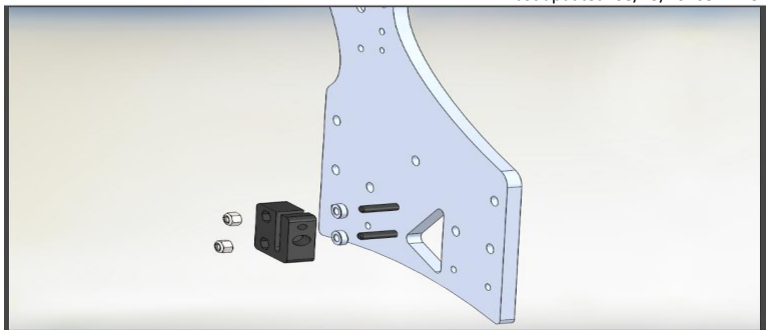
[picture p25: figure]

The ACME block is installed by using two M5 x 20mm bolts, 3mm spacers, and two M5 nuts. Do not over-tighten these M5 x 20 bolts, it is possible to collapse the block. Simply snug up and use lock-tight.

You can adjust the tension on the ACME block at this time if you so choose. Insert one of the ACME threaded rods into the block and adjust the set screw until there is slight resistance while trying to turn the ACME rod through the block. Do not overdo it. You can always adjust this after the build is complete.

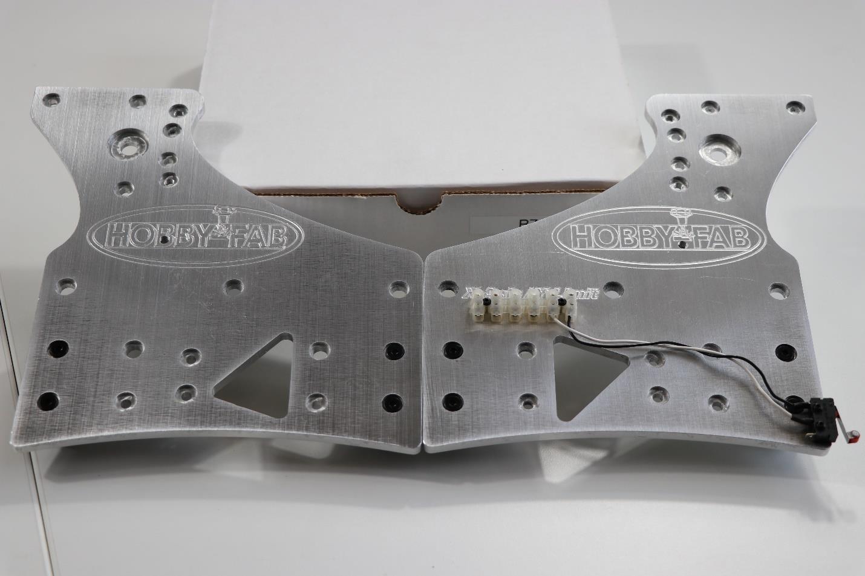
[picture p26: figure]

Last updated: 08/13/20108 Rev. 9

6

Limit switch and barrier block shown installed.

Last updated: 08/13/20108 Rev. 9

7

Step 2:

Step two has us assembling the front X/Z gantry plate. While looking at the completed machine, this will be the front plate that holds the Z gantry and moves side to side in the X direction. Recall front to back is Y and up and down is Z.

Note a change from the video, the Z is now driven by a single adjustable tension acme nut. Set the tension on the ACME as we did in step one. Insert the acme rod and turn in on the set screw until there is a slight resistance to turning the rod by hand. Do not lock the ACME in place by adjusting too far.

STEP 2 | Qty. | Smw3D | Builder
Front XZ Gantry Plate (Machined) | 1
Large Xtreme Wheels | 8
Mini Delrin Wheels | 8
Adjustable Tension Anti-Backlash Nut | 1
1/4" Spacers | 4
1/4" Mini Eccentric spacers | 12
3mm Spacers | 2
M5x20 | 2
M5x25 | 16

Note that all wheels are installed with ¼” eccentric spacers in this step to allow adequate room for the Z gantry.

To begin assembly, note that one side of the plate has recesses. We will be installing bolts from this side and the eccentric and regular spacers on the other side. Also, you will note one side of the inner gantry wheel holes is smaller in diameter, we call these the reference holes. Install these and tighten down the wheels, then use the eccentrics to add tension to the opposite wheels. All wheels on the reference holes should touch the beam, this ensures a true Z. Install and correctly tension the inner mini-wheels on the inside of the C-Beam (250 length), before installing the outer larger wheels. Install the eccentrics so that the wheels are as close as possible to the reference wheels. Install the beam and turn the eccentric until the wheel touches. Start in the center and work toward the top and bottom wheels.

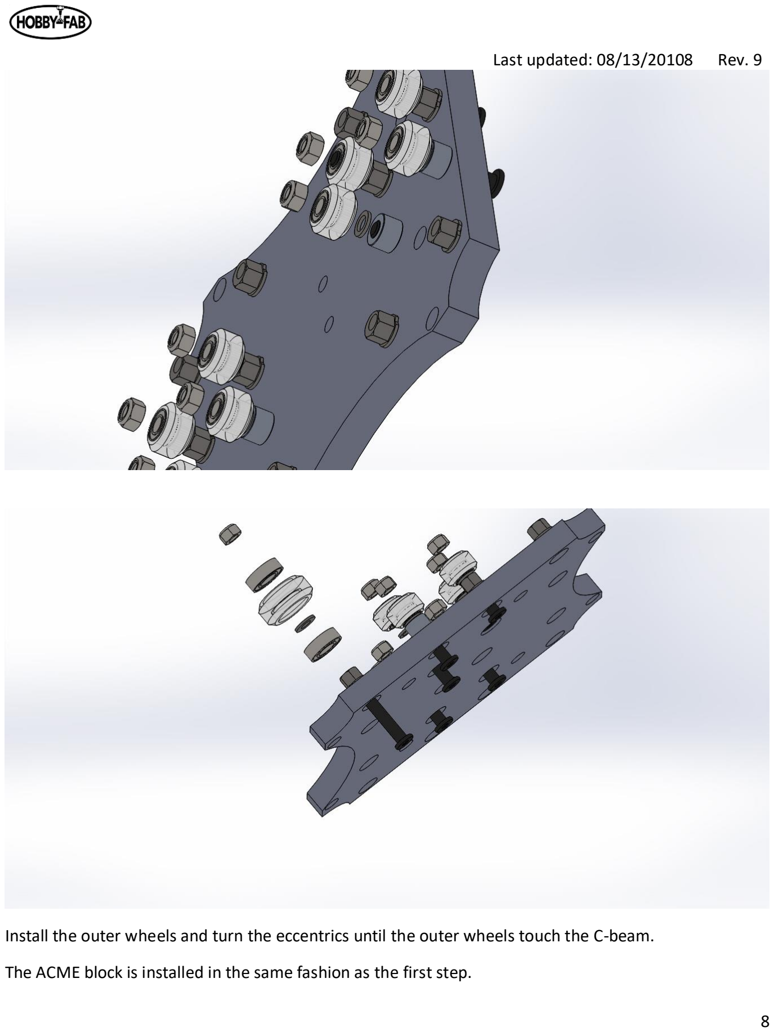
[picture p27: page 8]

Last updated: 08/13/20108 Rev. 9

8

Install the outer wheels and turn the eccentrics until the outer wheels touch the C-beam.

The ACME block is installed in the same fashion as the first step.

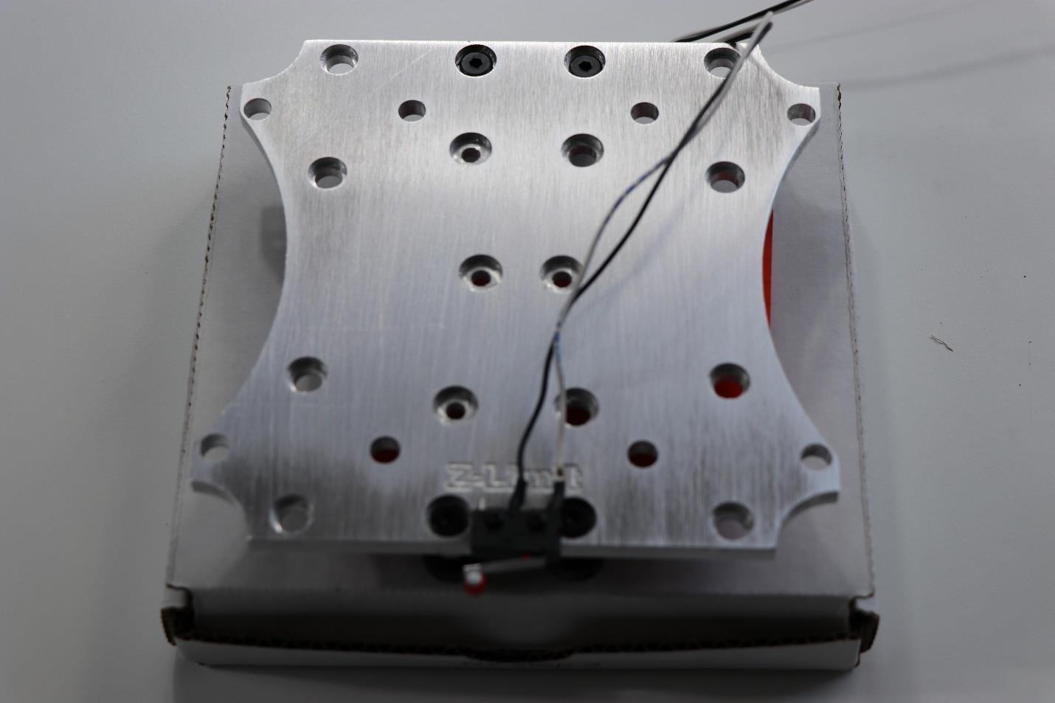
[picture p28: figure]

Last updated: 08/13/20108 Rev. 9

9

Note limit switch on bottom of plate, these wires will remain loose till install.

Last updated: 08/13/20108 Rev. 9

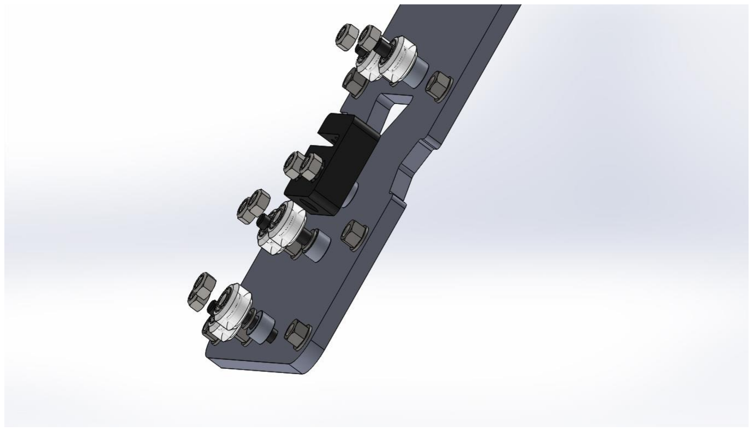
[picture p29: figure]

10

Step 3:

Step three will be the assembly of the rear X gantry plate. The same principles apply here. Use the reference wheels as a base and adjust the eccentrics to touch the inside of the sample beam (250mm length Z). Continue by installing the ACME block with the supplied 3mm spacers and M5 x 20mm bolts. Again, it is a good idea to adjust the tension on the ACME block at this time.

Note this plate is completely remodeled but the assembly remains the same.

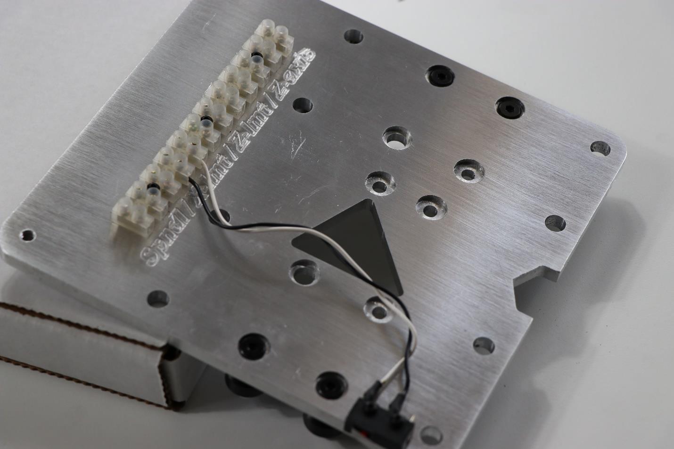
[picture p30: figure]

Last updated: 08/13/20108 Rev. 9

11

Notch in plate faces down. Limit switch on the left-hand side looking at the plate.

Last updated: 08/13/20108 Rev. 9

12

STEP 3 | Qty. | Smw3D | Builder
Rear XZ Gantry Plate | 1
Adjustable Tension Anti-Backlash Nut | 1
Mini Delrin Wheels | 8
3mm spacers | 2
m5x20 | 2
m5x25 | 8
6mm Spacers | 4
6mm mini eccentric spacers | 4

Last updated: 08/13/20108 Rev. 9

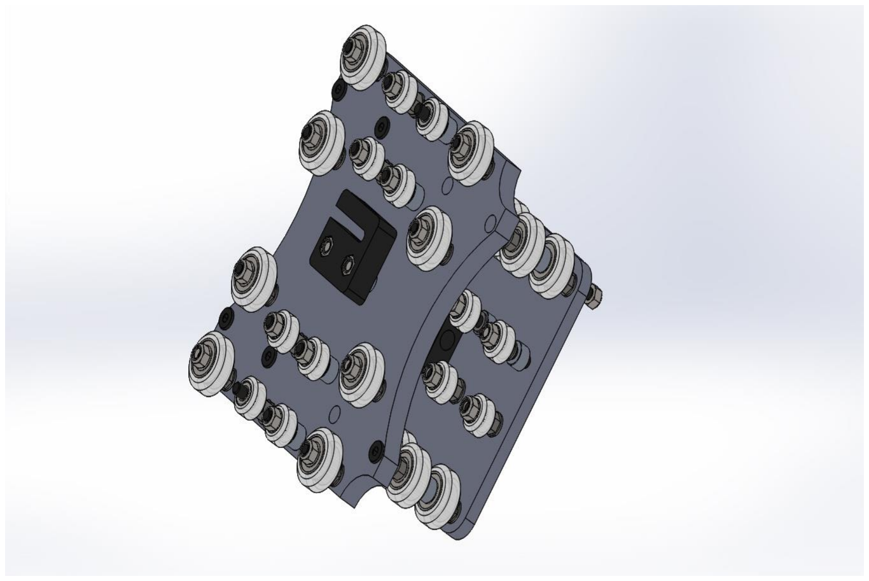
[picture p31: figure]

13

Step 4:

Step four will be the joining of the front to the rear X gantry plates. When you have all the large wheels in place, apply a light amount of tension on the M5 nuts to hold everything together. Then, adjust the eccentrics so that the wheels are as far away from the center of the X axis as possible.

Once the wheels are installed and eccentrics have them spaced out, slide your 250mm length C-beam in and adjust the tension evenly. Turn ⅛ of a revolution on the two eccentrics on one axle at a time. Start with the far-left top corner then go to the top right corner, then the right bottom, then the left bottom. If all are touching, you’re done. If not, repeat by turning each axle eccentrics ⅛ of a rev again. Once the outside wheels all touch, move to the inner wheels.

There are no shims used here except for those between the bearings on the wheel kit. The assembly is plate, eccentric, wheel, 9mm spacer, wheel, eccentric, plate.

Last updated: 08/13/20108 Rev. 9

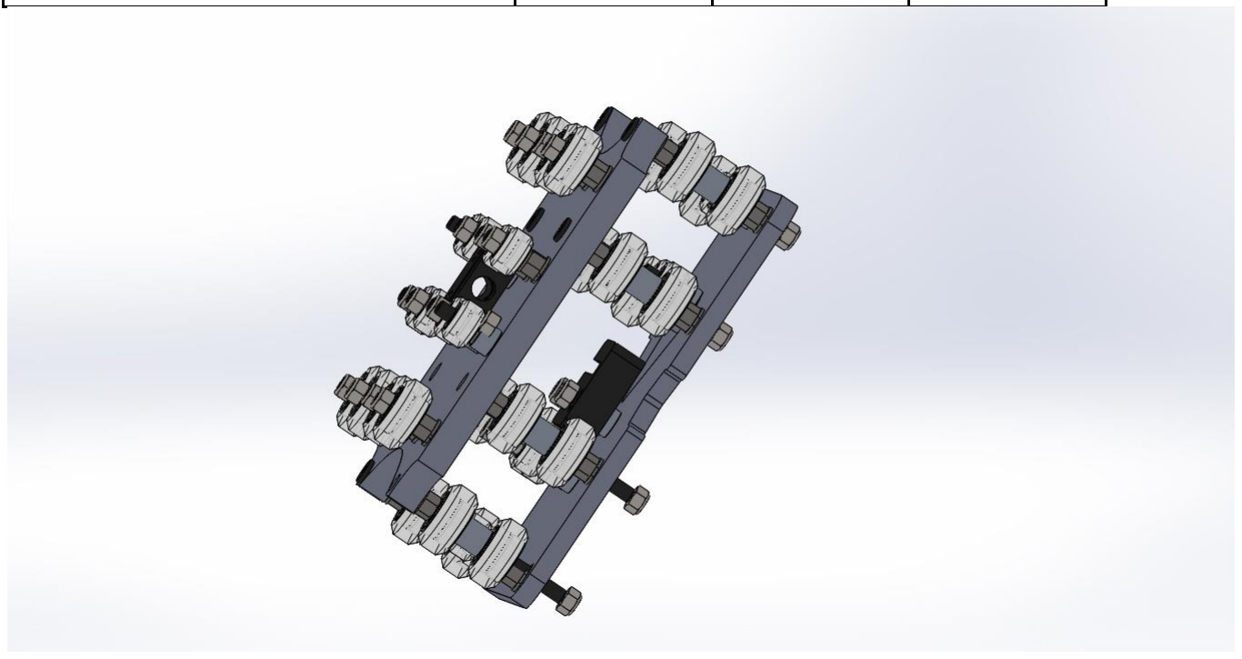
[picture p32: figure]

14

STEP 4 | Qty. | Smw3d | Builder
Large Xtreme Wheels | 16
9mm Spacers | 8
6mm Mini Eccentric Spacers | 16
M5x60 | 8

Last updated: 08/13/20108 Rev. 9

15

Step 5:

Step five we will mount the spindle to the Z gantry. The Z gantry will be the up and down axis of the machine. Note, the spindle clamp has been modified from the video. These spindle clamps are very fragile in the un-mounted state. Be cautious with these. Do not try to bend them or force them open with excessive force. Simply slide the clamp on the end of the C-Beam, install with a T-nut and M5 x 8 screw on both sides, and tighten. The clamp will be tight when installing the spindle. You can gently spread the clamp by hand and slide in the spindle. The clamps should be on the stainless caps of the spindle.

STEP 5 | Qty. | Smw3d | Builder
800w Spindle | 1
Spindle Clamps | 2
M5 T-Nuts | 4
M5x8 | 4
M5x35 | 2
250mm C-Beam | 1

Last updated: 08/13/20108 Rev. 9

16

Note, you can see both limit switches from the back view.

The Z-limit wires can now be moved directly up (in relation to the picture) and through the notch in the rear plate and inserted into the Z-Axis screw terminals.

Last updated: 08/13/20108 Rev. 9

17

Step 6:

Step six we will build the X gantry. Note, on the X gantry there will be a piece of 1000mm length C-Beam and a 1000mm length 20x20 V-Slot. The V-slot will be the exact same length as one piece of C-Beam. The ends of the beam will be colored to indicate the matching C-Beam and 20x20 aluminum V-slot. Please lay all out and find the piece of C-Beam that matches the 20 x20 x1000mm perfectly.

We will be mounting these two beams between the left and right Y gantry plates. We will also be mounting the first stepper motor to drive the X axis. The motor can be mounted on the left or right Y gantry plate. One should think about the final installation of the machine at this time and debate if there will be an advantage to the motor being mounted on one side or the other for space reasons. The M5x15mm bolts will hold the beams to the Y gantry plates. The bearings will fit into the recesses in the outside of the Y gantry plates. The ACME will thread through the anti-backlash nut on the X gantry we built in a previous step.

Prior to installation, it is advised to lightly sand down the ends of the ACME to allow the 608ZZ bearings to slide over the ends of the ACME. Only about .2mm need be removed from the OD of the final 40mm of both ends of the ACME. The bearings and ACME will be held in place by the 8mm lock collar on the end opposite of the motor, and the coupling on the motor side.

Install the X gantry on the C-Beam, thread the ACME through block on the X gantry, then install the two side plates with the provided M5x15mm bolts.

Last updated: 08/13/20108 Rev. 9

18

STEP 6 | Qty. | Smw3d | Builder
M5x15 | 10
M5x55 | 2
1.5in spacers | 2
608ZZ Bearing | 2
8mm lock collar | 1
6.35x8 Coupler | 1
1000mm Acme | 1
1000mm 20x20 | 1
1000mm C Beam | 1
NEMA 23 2.8A | 1
Shim: 12.5x8x1.5 | 2

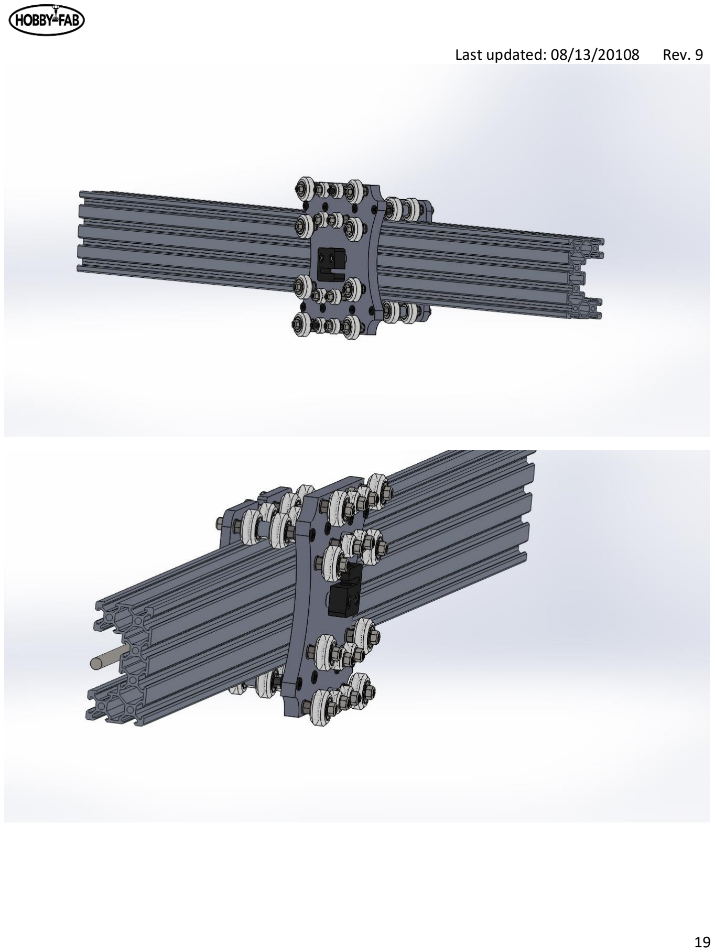
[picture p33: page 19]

Last updated: 08/13/20108 Rev. 9

19

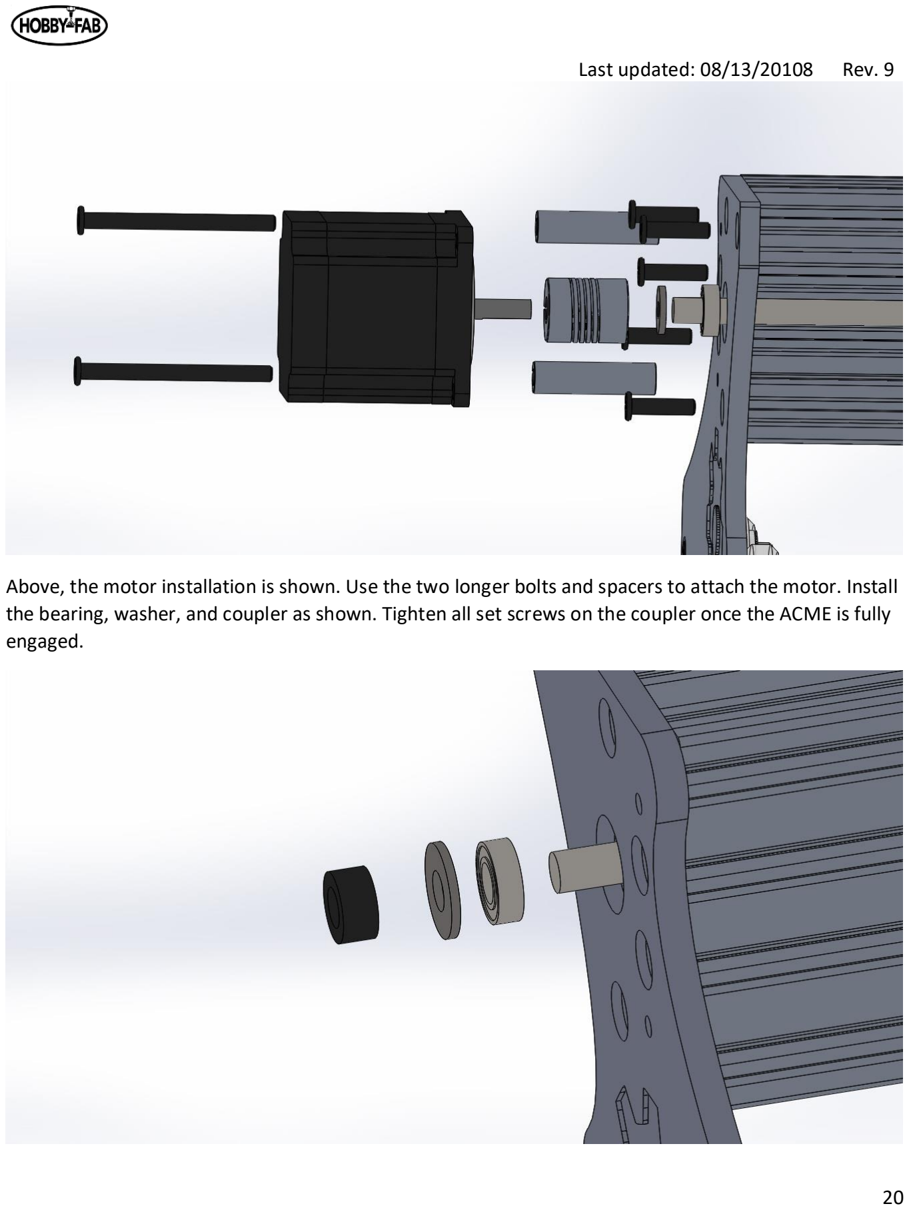
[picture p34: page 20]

Last updated: 08/13/20108 Rev. 9

20

Above, the motor installation is shown. Use the two longer bolts and spacers to attach the motor. Install the bearing, washer, and coupler as shown. Tighten all set screws on the coupler once the ACME is fully engaged.

Last updated: 08/13/20108 Rev. 9

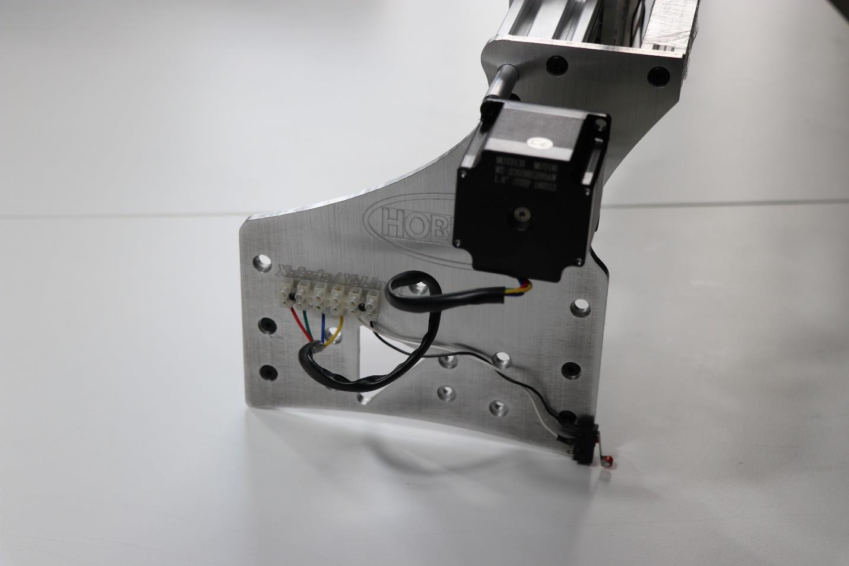
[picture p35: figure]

21

The opposite side is constrained by the lock collar. In the step seven bag you will find an ACME nut plate. Use this to push the lock collar flush against the bearing and remove any slack from the drive. Excessive force is not needed. Simply tighten down the nut plate while holding the coupler on the other end, then tighten the set screw. Remove the nut plate afterward.

Last updated: 08/13/20108 Rev. 9

22

Step 7:

Step seven will be the build of the Y gantries. Your machine is really going to take shape after this step. This step is much of a repeat of the last, but we will be mounting end caps instead of Y gantry plates.

Step 7 | Qty | Smw3d | Builder
NEMA 23 2.8A | 2
6.35x8 Coupler | 2
Machined end corner caps | 4
Lock collar | 2
608ZZ | 4
C-Beam 1000mm | 2
1.5" spacers | 4
M5x55mm bolts | 4
M5x20mm bolts | 20
Single corner bracket | 4
M5 nuts | 4
1000mm ACME | 2
ACME flange nut | 1
Shim: 8mm | 4

Each corner bracket holds the ACME in place and retains the build to the board.

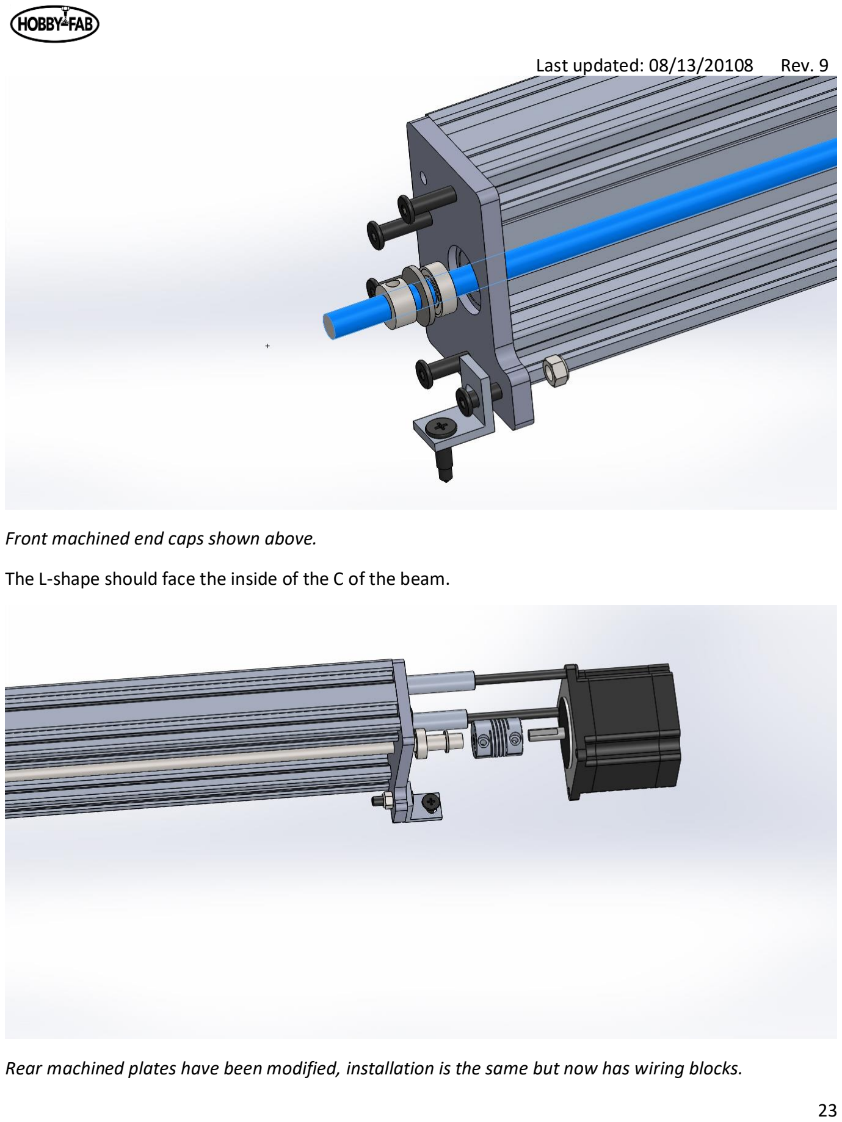
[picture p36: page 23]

Last updated: 08/13/20108 Rev. 9

23

Front machined end caps shown above.

The L-shape should face the inside of the C of the beam.

Rear machined plates have been modified, installation is the same but now has wiring blocks.

Last updated: 08/13/20108 Rev. 9

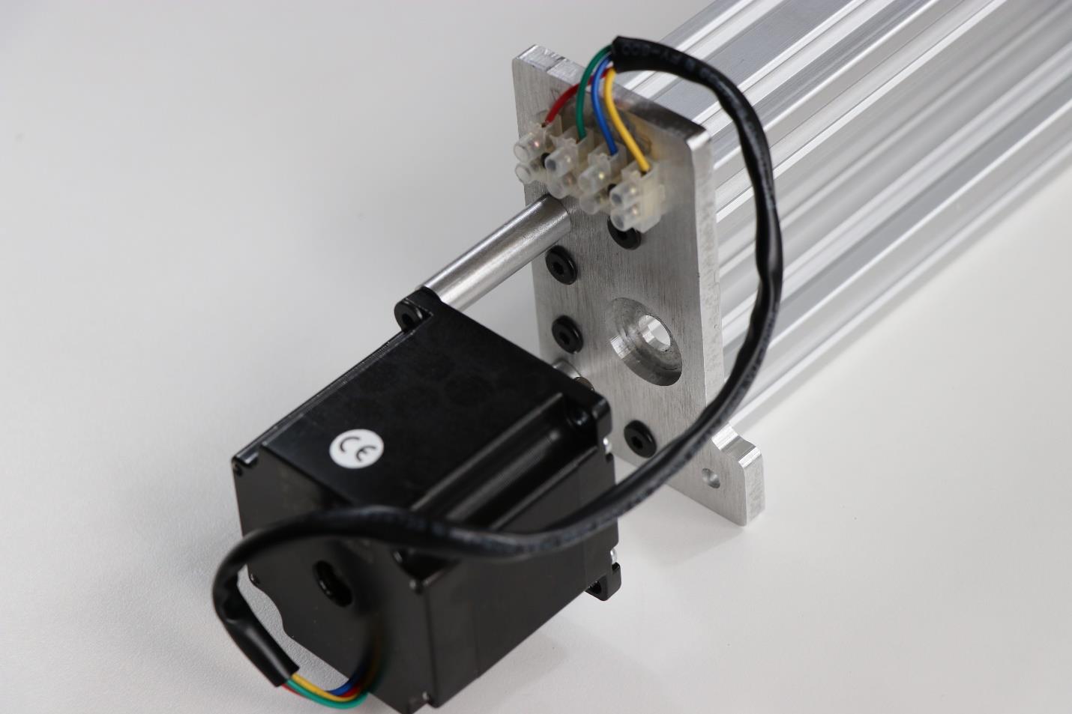
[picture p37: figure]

24

It is best to install the wood screws into the spoiler board near the last step when we can square the build. If you choose to install them now, thread the ACME in until the Y gantry plates are the same distance from the corner plates. Then, install the corner plates square with the front edge of the spoiler board.

Y rear machined end plates

Last updated: 08/13/20108 Rev. 9

25

Step 8: We will assemble the full Z gantry in this step. Grab the Z gantry with the spindle and prepare to install this with the 250mm ACME. This axis is in compression versus the previous tension set-ups.
Step 8 | Qty | Smw3d | Builder
C-beam end plates | 2
M5x55mm | 2
1.5" spacers | 2
250mm ACME | 1
688zz | 2
6.35mm x 8mm coupler | 1
Nema 23 | 1
M5x25mm | 8
8mm Lock Collar | 2
Shim:12.5x8x1.5 | 2

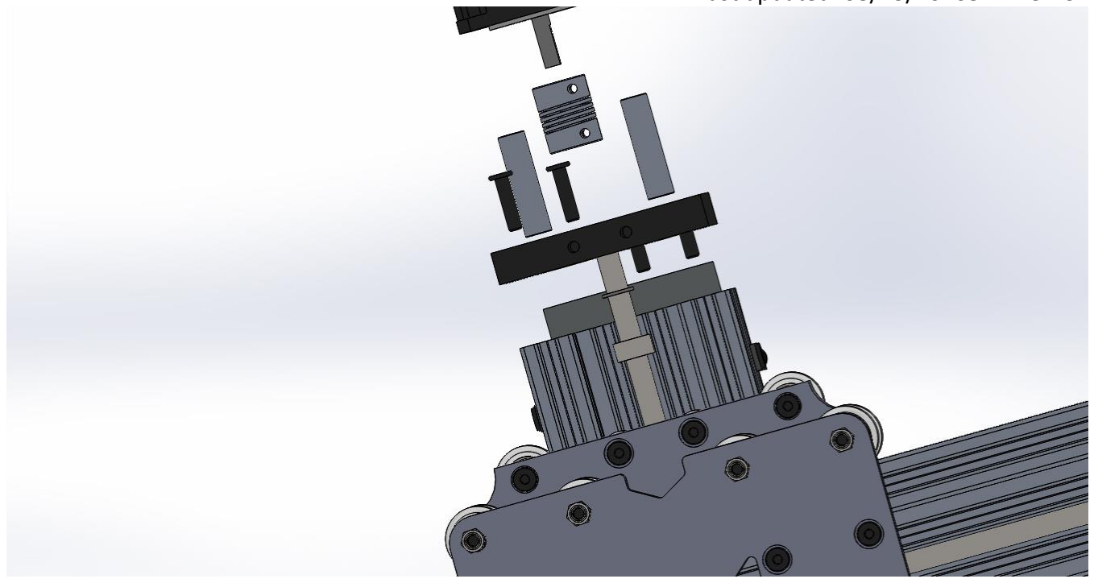
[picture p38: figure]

Last updated: 08/13/20108 Rev. 9

26

Thread the ACME through the anti-backlash nut, then slide the lock collar, bearing, and shim over the top. Attach one of the black plates on the top of the Z via the supplied M5 x 25mm bolts. Feed the Z gantry down through the wheels in the front of the X axis. Continue to slide down until there is enough ACME hanging out of the top of the plate to fully engage the coupling. Set this height by tightening the lock collar on the ACME and trap the shim and bearing into the recess on the plate. Attach the motor as in the previous step. On the lower portion, perform the same task. Slide a lock collar, bearing, and shim, then the plate over the bottom of the ACME. Lock the axis in place by tightening the set screw on the lower lock collar.

Watch the play in the Z final assembly. You should not be able to wiggle the spindle up and down. Sometimes it is easier to leave a slight gap between the C-Beam and the end plate, then slide the lock collar all the way down, lock in place, then tighten the 4 qty. M5x25mm bolts. Do not overly compress the ACME. A very small gap of about .01mm is all that is needed when tightening the axis to remove play.

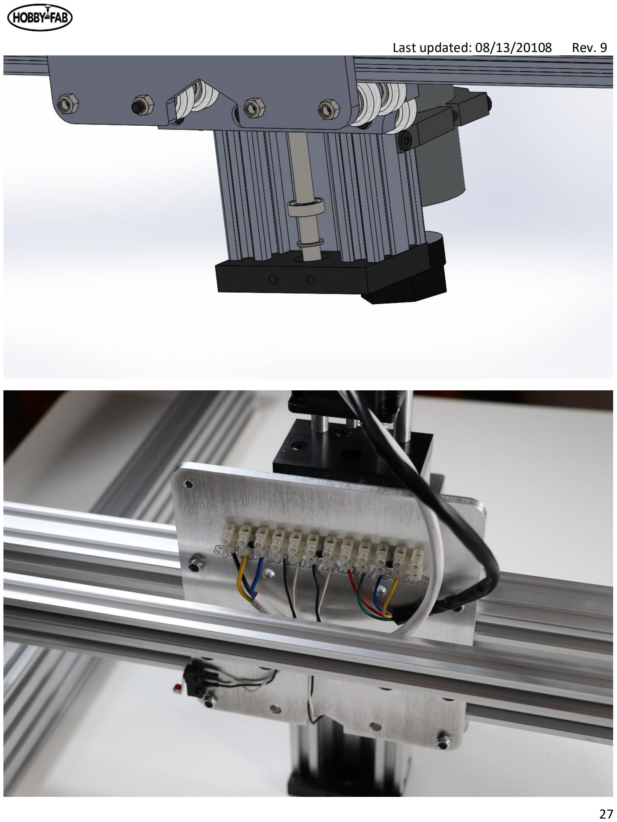
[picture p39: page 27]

Last updated: 08/13/20108 Rev. 9

27

Last updated: 08/13/20108 Rev. 9

28

Last updated: 08/13/20108 Rev. 9

29

Step 9: Let us add some peripherals.
Step 9 | Qty | Smw3d | Builder
3/16" ID 5/16" OD vinyl tubing | 30
4 pole wire 18 to 22g | 36
3 pole wire (typically 16g) | 18
15mmx30mm cable chain | 2
M5 drop-in T-nut | 1
M5 x 10mm bolt | 1
9mm spacer | 2
Water pump | 1
M5x20mm bolt | 1
Sheathing 10mm | 10
M5 x 25mm bolt | 1
Figure out where you want your electronics and water reservoir. It is highly advised they are not in the same location.

Run the cable chain down either the left or right side of the build. Mount one end to the y gantry plate. One plate will have a threaded hole in the middle of the hobby-fab logo, this is for the Y cable chain. Reduce the Y cable chain to half the shipped length. You will need to remove one end of the cable chain. If you remove the proper end, you will be left with a hole in the side of the cable chain where the mount end was “tabbed” in. Use this hole, a 9mm spacer, and M5x20mm bolt. Mount this end upside down and cable chain extending facing the front. Mount the other end right side up with a wood screw to the spoiler board, again aimed towards the front.

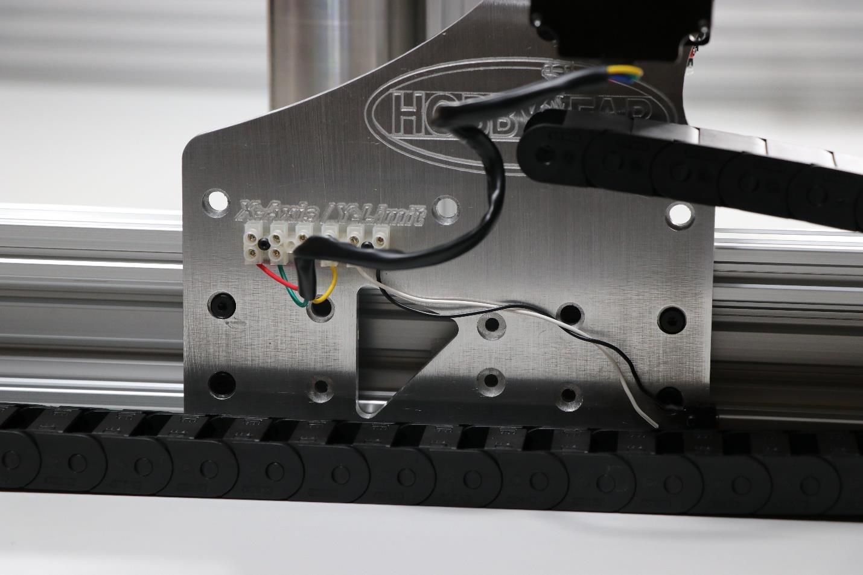
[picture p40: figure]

Last updated: 08/13/20108 Rev. 9

30

Last updated: 08/13/20108 Rev. 9

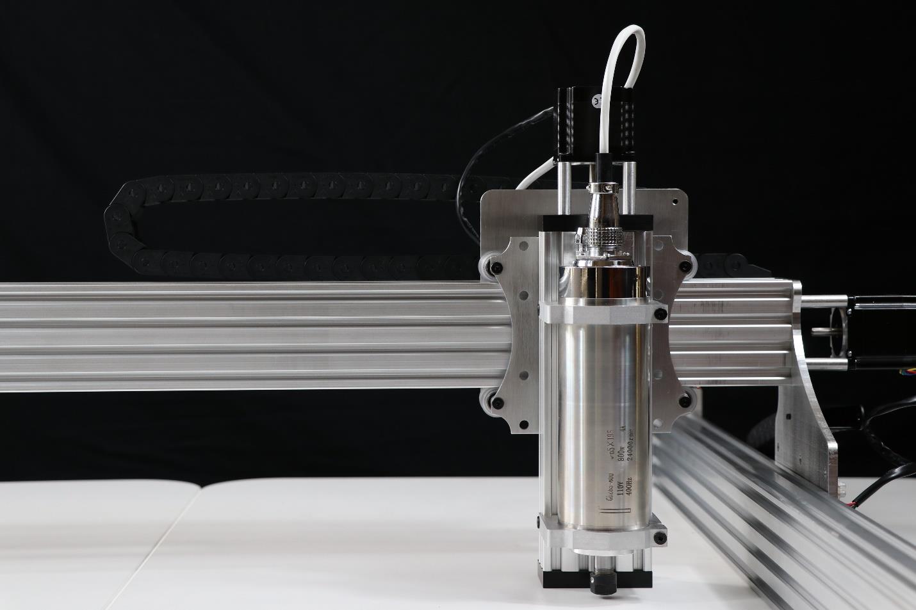
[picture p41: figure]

31

Mount the X cable chain in the same method. Attach the upside-down end to the back of the Z gantry. There is a threaded hole in the upper corner of the rear plate. Use two 9mm spacers and the M5 x 25mm bolt, attach the other end to the top of the 20x20x1000mm v-slot with the drop-in tee-nut and M5x10mm bolt.

At this time, it is best to remove the cable chain tops, as we will route wires and cooling hoses through both.

Install the water tubing by taking the nuts off the top of the spindle. Install a hose and route through both cable chains to exit at the rear of the machine. Route a hose to your tank and attach to the top of water pump. Route another hose to the tank and allow to flow into the tank. The video R7v9 provides a good example of a tank you can use. If your tank is a good distance away, you can pick more tubing up at most home improvement stores it is 3/16 ID by 5/16 “ OD.

Install the three wires from the spindle to the terminal block on the back of the rear X gantry plate.

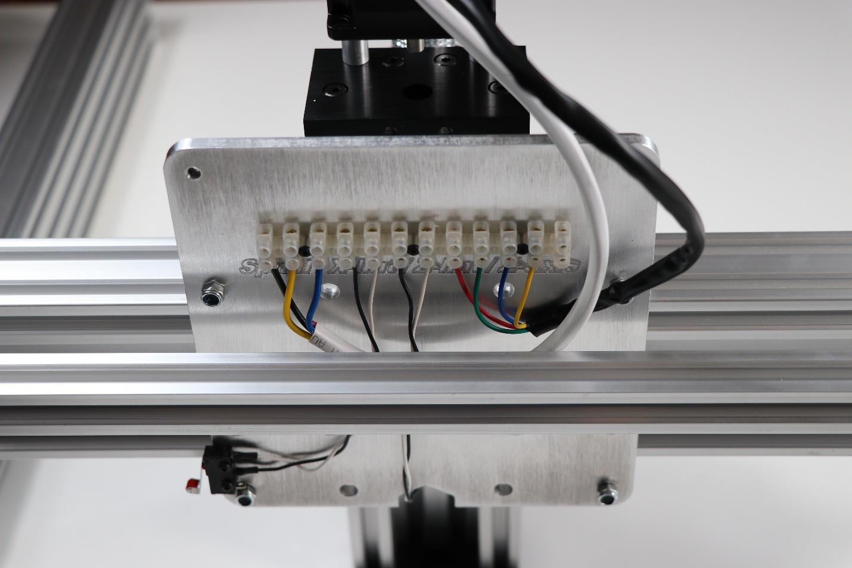
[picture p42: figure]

Last updated: 08/13/20108 Rev. 9

32

Last updated: 08/13/20108 Rev. 9

33

Step 10:

You have made it! The final step is the electronics of the kit. This video is rather short, so when you have questions hit the G+ group up and the team of builders will be happy to assist!

The video is meant for builder that purchase the all in one control box. See the end of this document for detailed instructions.

https://youtu.be/cOv-T105RK4

Communicating with the machine:

If you have the all in one PRO control box communication is held internal to the machine. Use the video and instructions at the end of this document.

If you have the all in one simple control box, you will need a computer and follow these directions.

Plug a USB cable A to B into the control box.

Start your computer and open a google chrome window.

Go to this address:

https://cnc.js.org/docs/desktop-app/

Download the appropriate desktop app for your system, OS, windows, etc.

Open CNC.js

Look for a connection window on the top left hand side.

Power the machine.

Under port, hit the refresh button, use the drop down to find the USB port.

A blue button labeled “Open” is also in the connection window. Click this button.

You should now be connected. You must home the machine prior to jogging around. There is a blue button labelled “Homing” in the upper right-hand corner, click this.

The machine should raise the Z, then lower a bit, then go back up. X and Y axis should follow.

Once homing is complete you can now jog around.

If you jog the wrong direction, you will lock grbl. The system purposely does this to avoid damage. If locked, simply hit the refresh and unlock buttons located near the homing button.

You are now connected to the machine and it is fully usable!

Last updated: 08/13/20108 Rev. 9

34

You can try jogging around, homing the machine, starting the spindle (M3 S1000), etc.

Take time to familiarize yourself with this window. There are a lot of features here. If you want to jog the machine around go to the upper right-hand window, called Axes, click the down button and the box will expand. Click on the “move” tab and select “1”

Then click any of the direction buttons. The machine should move.

GRBL Settings change:

Example

If an axis such as X, Y, or Z moves in the opposite direction it should you will need to change the “$3” mapping. For an understanding of this see the GRBL page:

https://github.com/grbl/grbl/wiki/Configuring-Grbl-v0.9

Scroll down a bit and you will see a set of numbers “$1” through “$132”, below this is an explanation of what each does. Related to the example above, if X moves the opposite direction we tell it, we would
need to set “$3=1” based on this information:
Setting Value | Mask | Invert X | Invert Y | Invert Z
0 | 00000000 | N | N | N
1 | 00000001 | Y | N | N
2 | 00000010 | N | Y | N
3 | 00000011 | Y | Y | N
4 | 00000100 | N | N | Y
5 | 00000101 | Y | N | Y
6 | 00000110 | N | Y | Y
7 | 00000111 | Y | Y | Y

To make changes, go to the Com screen. Look in the mid-left-hand side of the screen. Note it is black with white text.

At the bottom of this box you will see an area where you can type things, type in this box, $$

Last updated: 08/13/20108 Rev. 9

35

You will see what your current settings are. Only if an axis is going the wrong direction should you make the below change.

Note that $3=0 out of the list of things there.

Type $3=1

Then type $$

Note that now in your list $3=1, and when you jog the machine X now moves in the opposite direction. If all axis move in the wrong direction you would type $3=7, for example.

One last thing to check is that the spindle turns the right direction. Type M3 S12000 in the serial port. This should turn the spindle on at 12000 RPM. Type M5, the spindle stops. Looking down at the top of the spindle, it should turn to the right.

The machine is set up and ready to be used! Play around with the $ settings. Set travel limits, set max velocities and accelerations.

Have a read on our page about “How to CNC” here: https://www.smw3d.com/blog/how-to-cnc/

Read about feeds and speeds here: https://www.smw3d.com/blog/what-is-the-right-feeds-and-speeds-for-my-cnc-router-kit/ (https://www.smw3d.com/blog/what-is-the-right-feeds-and-speeds-for-my-cnc-router-kit/)

Explore the machine, explore software, explore all that various things you can create. There is so much to learn and new opportunities around every corner when you can build the world around you.

Join us and show off your build on the R7 Google Plus page. We look forward to the amazing things you will build!

Last updated: 08/13/20108 Rev. 9

36

# Laser install instructions

2.8w laser add on is identical for OX and R7.

If opted for during purchase a J-tech 2.8w complete laser system will be added to the order.

Safety:

Please open this package and carefully read and understand the safety warnings associated with this product included in the package.

Lasers are dangerous, fire hazards and eye safety should always be the end user’s top priority when using the laser add on feature.

Never leave the laser unattended when in operation!

Always wear the safety glasses provided in the kit when using the laser diode add on. If more than one party is in the local vicinity they should also have the required eye protection.

It is suggested to keep fire suppression equipment close at hand and prepared for an emergency.

SMW3D, Hobby-Fab, J-Tech and affiliated groups hold no liability to property, personal, or any other damage created from the use of this product. The purchase and use of this laser add on system is strictly the end user’s liability and responsibility to ensure safe use.

Specifications:

Please see the J-tech instruction manual for full details.

https://jtechphotonics.com/wp-content/uploads/2013/05/Instruction-Manual-445nm-Laser-Diode-Component-9mm-G2-Lens-J-Tech-Photonics-Inc.-v2.pdf

Bill of Materials:

- 2.8w J-tech laser system with extended wires
- Modified spindle clamps
- 2 quantity M3 x 12mm bolts

Installation:

Last updated: 08/13/20108 Rev. 9

37

The spindle clamps in your kit will have 2 additional holes tapped into the side of one of the spindle clamps. There will be two bolts pre-installed in the spindle clamp.

This clamp will be the lower clamp on the spindle closer to the collet side of the spindle.

Shown above on the 400-watt spindle, 600w and 800w are identical.

These holes should center the laser in the Y plane with the spindle center.

Open the laser package and look for a small bracket that will fix a fan to the back of the diode laser.

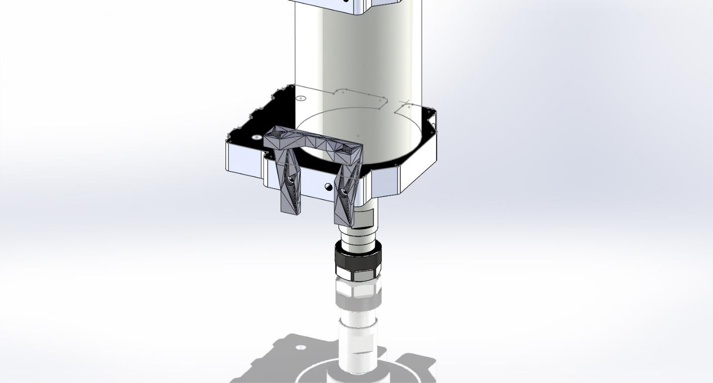
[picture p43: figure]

Last updated: 08/13/20108 Rev. 9

38

Install the laser diode with this bracket. The laser should face downwards with the fan mounted on the bracket with the Sunon logo facing the diode. It is advised to install the laser M3 bolts with blue thread lock.

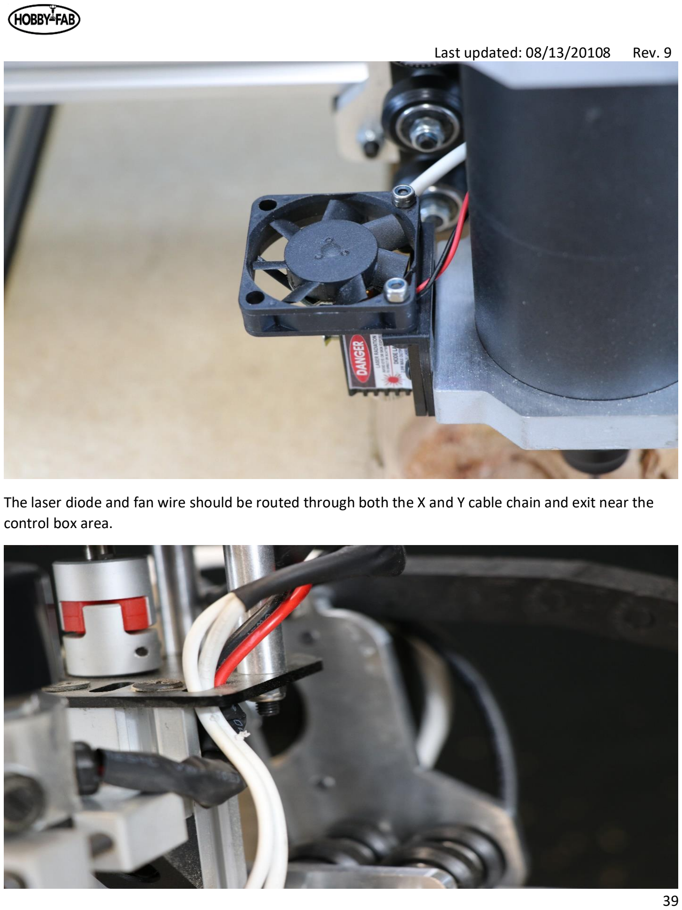
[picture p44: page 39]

Last updated: 08/13/20108 Rev. 9

39

The laser diode and fan wire should be routed through both the X and Y cable chain and exit near the control box area.

Last updated: 08/13/20108 Rev. 9

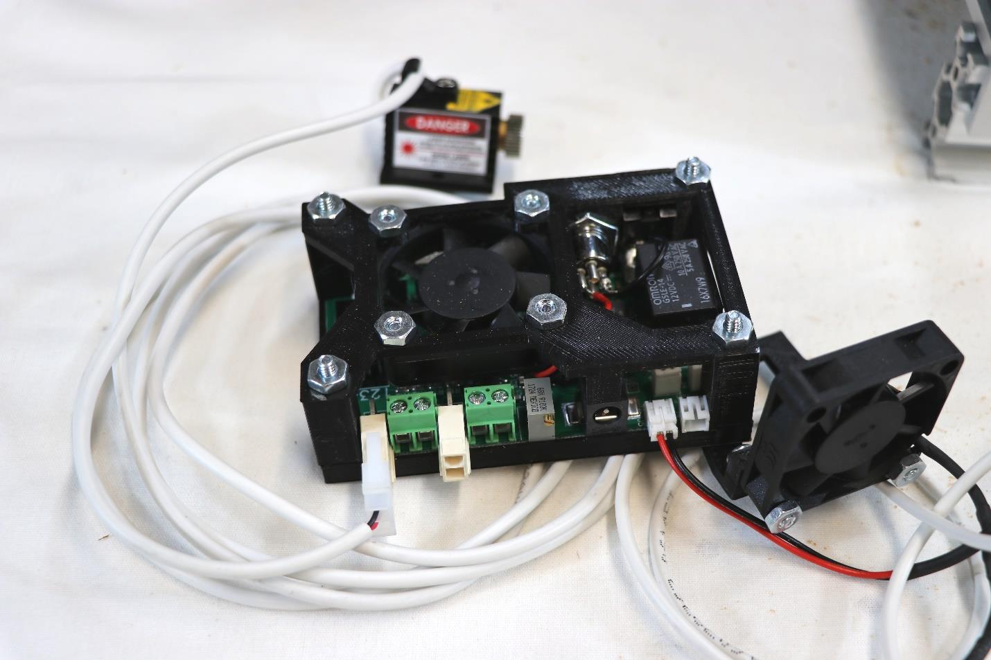
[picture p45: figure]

40

The laser diode will connect to the driver board on the H3 header and the fan will connect to the fan header.

1 Shown uninstalled for relation

Next connection will be the PWM signal. Regardless of the GRBL controller sent we will utilize the PWM + and – signals to control the laser power.

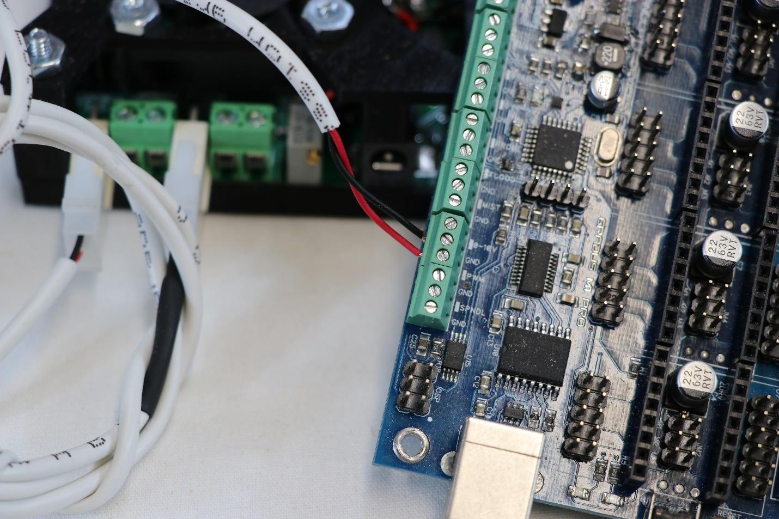
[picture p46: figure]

Last updated: 08/13/20108 Rev. 9

41

Connect the bare ended wire with the molex connector on the opposite side next to the laser connector, connect the other end to the PWM positive and negative connections on the board. Polarity matters. On the all in one controller the accessory port, yellow is PWM +, blue is PWM -.

Connect the supplied power supply with the barrel connector to the laser driver board.

The laser add on is now ready for use.

Last updated: 08/13/20108 Rev. 9

42

Use:

When the laser driver board is powered for the first time, every use, the reset button must be pressed.

Insert the safety key, turn on the power and press the rest button. The fans should both come on along with a green LED indicating the driver board is ready for use.

Vector Gcode can be created in the same fashion as we create routing Gcode. A spindle speed of 4000 (lowest setting on most our products) will be the minimum power. A spindle speed of 12000 will be maximum power.

Raster jobs are best created by other software than the ones we use for routing gcode generation. They provide more efficient code.

Once gcode has been created, load gcode into your communication software, such as CNC.js or bCNC. Locate the serial port box, in CNC.js this is the black box in the middle of the left-hand side of the screen. bCNC this is the upper right-hand corner of the screen, a tab called terminal.

Type $$ and hit enter.

Note that $32=0 currently. Router control is standard in this mode. Type $32=1 and hit enter. The machine is now in laser mode.

Making this setting change turns off the spindle power, hence the laser power during G0 moves and enables during G1, G2, G3 moves.

As an example, in code G0 X1 Y1 Z1 the laser will be off moving or rapid to this location. The next move F600 G1 X2 Y2 Z2 will turn on the laser and move to this location. The next rapid of G0 will turn off the laser.

The power of GRBL allows the use of standard routing gcode to be used in this method without the need for special commands to operate the laser.

Last updated: 08/13/20108 Rev. 9

43

Focus Length and Gcode generation:

The J-Tech diode has a focus length of around 3” from the factory. When setting the work piece home use a tape measure or calipers to ensure the diode is this distance away from the work piece. Set this as your Z=0.

When producing gcode for laser use, use a very small Z depth of cut (DoC) such as .001 units. Also, clearance height can be reduced to 0 for maximum efficiency.

The number one mistake we make here is forgetting to turn the machine back to router mode. After laser operations recall to set $32=0.

Any questions please do not hesitate to contact us we will happy to assist.

Contact@hobby-fab.com

Last updated: 08/13/20108 Rev. 9

44

Please read this entire document before installing and using the all in one control box.

## WARNINGS:

Do not connect the 110VAC power cable till all motors are connected.

Do not disconnect any stepper motors while the control box is powered.

Mount the box to something non-conductive. A ground loop (https://en.wikipedia.org/wiki/Ground_loop_(electricity)) can be created between the box and machine if connectivity is allowed other than intended connections.

Do not place any electronics on top of the control box including 600w PSU/ESC, etc. The noise will cause erratic behavior.

Do not open the control box, wires can be dislodged.

If the shipping box is severely damaged upon receipt please DO NOT PLUG THE BOX INTO A WALL OUTLET. The box is internally grounded and fused for both AC and DC but your safety is top priority, a damaged box should not be used. SMW3D, Hobby-Fab and related affiliates hold no responsibility for damage to equipment or persons by using this product. Be safe, be smart, build!

## CARE:

The control box is made of cold rolled steel and the early units have a black oxide coating. This is a similar process to bluing a firearm. In the same sense the outer surface of the box can be protected in the same manner. Using any type of firearm protectant or light oil will protect the box from rusting. Avoid spraying the box with an aerosol, instead spray a rag and wipe the box down.

# Hobby-Fab Controller

Last updated: 08/13/20108 Rev. 9

45

## Connections:

Step 1:

Connect all stepper motors to the X, Y, (if using a gantry style machine Y2) and Z. The 6 pin connectors are labelled below. Looking at the face of the box the connections are, from left to right:

Accessories :

Black/ White = Z probe | Yellow/Blue = (+/-) PWM | Red/Green = (+/-) 0-
10V

X Axis:

Black/White = X axis limit switch Yellow/Blue = 1A 1B stepper motor pair Red/Green 2A/2B

Y Axis:

Black/White = Y axis limit switch Yellow/Blue = 1A 1B stepper motor pair Red/Green 2A/2B

YNL: (this is only needed on gantry style machines with two Y motors)

YNL stands for Y axis no limit, the black and white wires are not present on this axis.

Yellow/Blue = 1A 1B stepper motor pair | Red/Green 2A/2B

Z Axis:

Black/White = Z axis limit switch Yellow/Blue = 1A 1B stepper motor pair | Red/Green 2A/2B

NOTE: If your machine is a kit from us this will directly plug (color to color) into the stepper motors and limit switches.

NOTE: All limit switches are filtered and should be used in the NO (Normally Open) position.

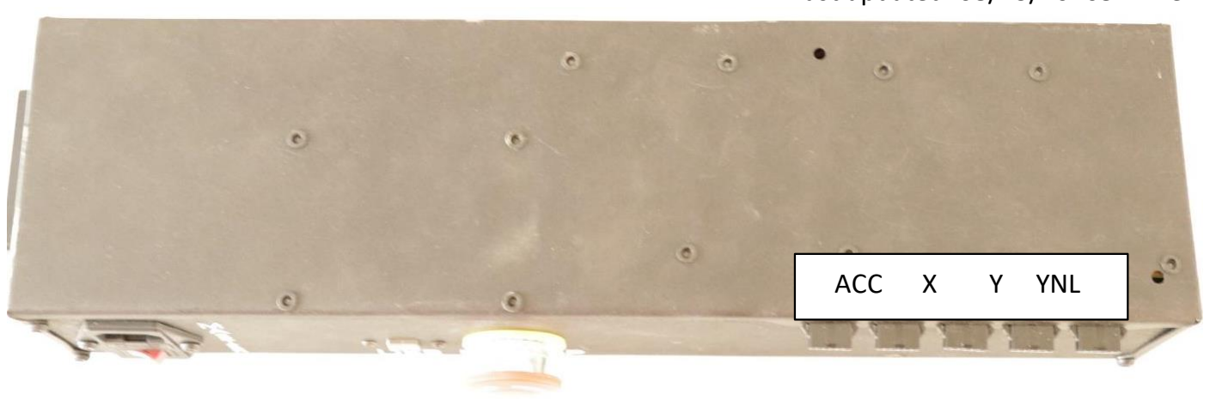
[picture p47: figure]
ACC; Y YNL

Last updated: 08/13/20108 Rev. 9

46

Step 2:

Make sure the E-Stop is “out” this allows power to the control board.

Step 3:

Plug in a USB style Mouse and Keyboard (https://www.amazon.com/Computer-Keyboard-Mouse-Combos/b?ie=UTF8&node=1194464) to either USB port on the front.

Step 4:

Plug an HDMI monitor into the port on the face.

Step 5:

Plug the 110VAC cable into the fused connection on the far left.

Step 6:

Turn on the master switch.

Last updated: 08/13/20108 Rev. 9

47

## USE:

Every control box is tested prior to shipment. Based on your machine some changes may be required prior to use.

E-stopping the box kills power to the motors, but does not remove power to the program. In the event of an issue, one should be able to retain the current program and restart after homing.

There are two 110VAC outlets on the front of the box, next to the AC power in. The upper plug is a fused direct 110VAC plug, do not plug anything over 5A into this outlet. The lower plug is controlled by M8 commands. Typing M8 in a program will deliver 110VAC to this plug, typing M9 will remove power to this plug.

Settings may need to be modified prior to use. When plugged in the monitor will display a logo while boot up is taking place. Once this splash screen is complete the system will open to bCNC (https://github.com/vlachoudis/bCNC) and connect automatically.

THE MACHINE MUST BE HOMED PRIOR TO JOGGING

There is a home button on the control tab at the upper left-hand corner. Click home.

You should expect the Z axis to go up, touch the limit switch, go down, then come back up. After this action X and Y should both start moving towards the limit switches.

If the machine does not move in the correct direction. Click the unlock and reset button in the upper left-hand corner of the file tab. This will stop all motion.

Go to the upper right-hand corner and find the terminal tab.

Click on this.

A serial port message box will be on the left-hand side of the screen with an area to type in at the bottom.

Type $$

These are your GRBL Settings (https://github.com/gnea/grbl/wiki/Grbl-v1.1-Configuration) you will need to invert the Z if it went the opposite direction. This is done by typing $3= (some number that corresponds below)

Last updated: 08/13/20108 Rev. 9

48

Setting Value | Mask | Invert X | Invert Y | Invert Z
0 | 00000000 | N | N | N
1 | 00000001 | Y | N | N
2 | 00000010 | N | Y | N
3 | 00000011 | Y | Y | N
4 | 00000100 | N | N | Y
5 | 00000101 | Y | N | Y
6 | 00000110 | N | Y | Y
7 | 00000111 | Y | Y | Y

For instance, when you typed $$ and hit enter, and your current $3=1 and your Z was going the wrong direction, try $3=6 hit enter.

Try homing the machine again. Continue the above till all 3 axis are homed.

Post the above exercise and homing you are ready to CNC.

Play around inside bCNC and read more at the links provided within this document.

Setting workpiece zero is as simple as jogging to the location and clicking the X=0, y=0, z=0 buttons on the control tab below the digital readouts.

Last updated: 08/13/20108 Rev. 9

49

Please email or call if there are any issues we are happy to assist.

contact@hobby-fab.com or 346-333-6500.

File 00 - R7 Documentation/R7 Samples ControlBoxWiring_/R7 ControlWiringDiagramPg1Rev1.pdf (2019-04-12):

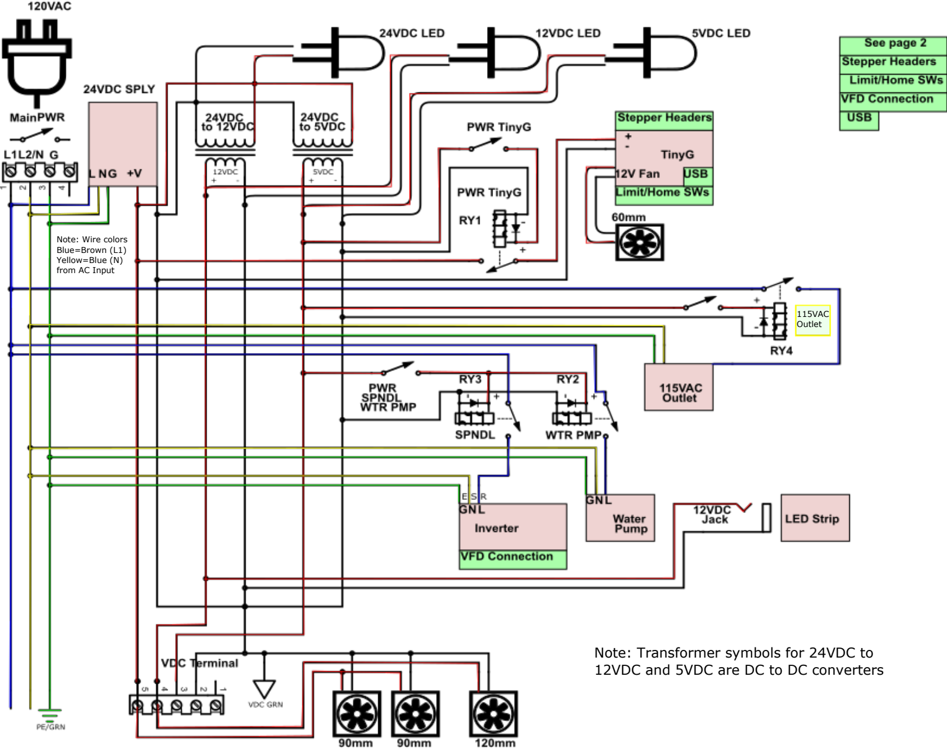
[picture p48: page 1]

115VAC
Outlet

Note: Wire colors
Blue=Brown (L1)
Yellow=Blue (N)
from AC Input

Note: Transformer symbols for 24VDC to 12VDC and 5VDC are DC to DC converters

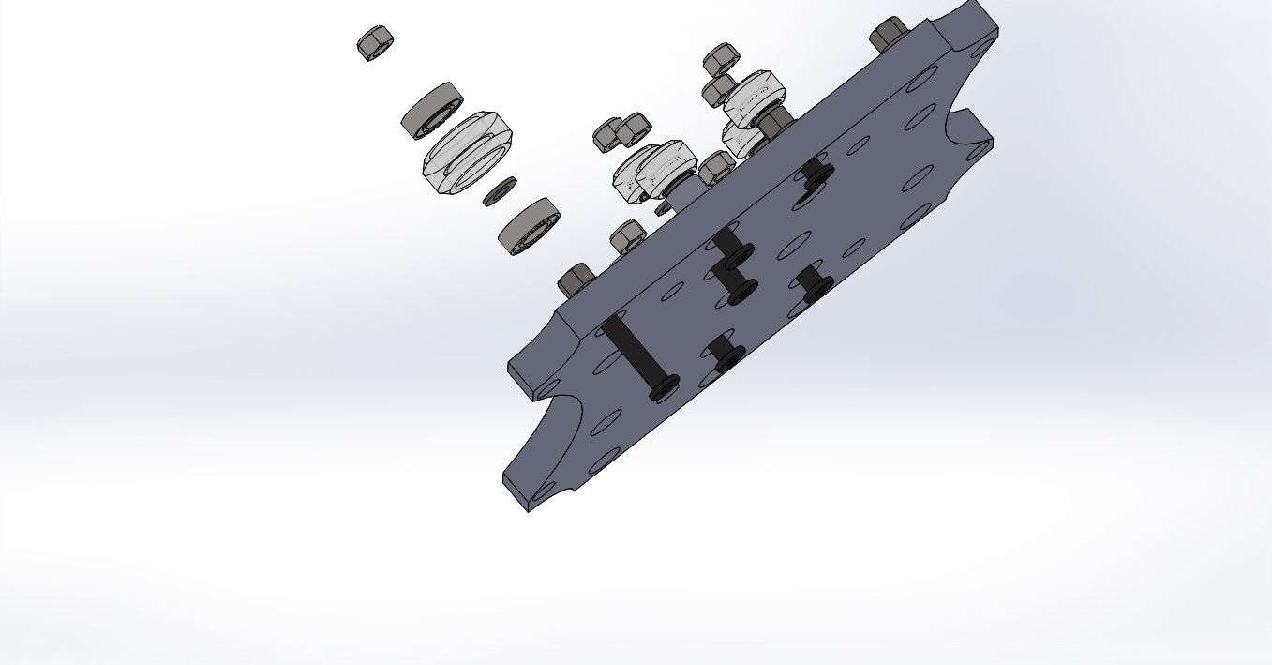
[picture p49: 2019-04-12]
00 - R7 Documentation/Images/Step 2 R7.JPG

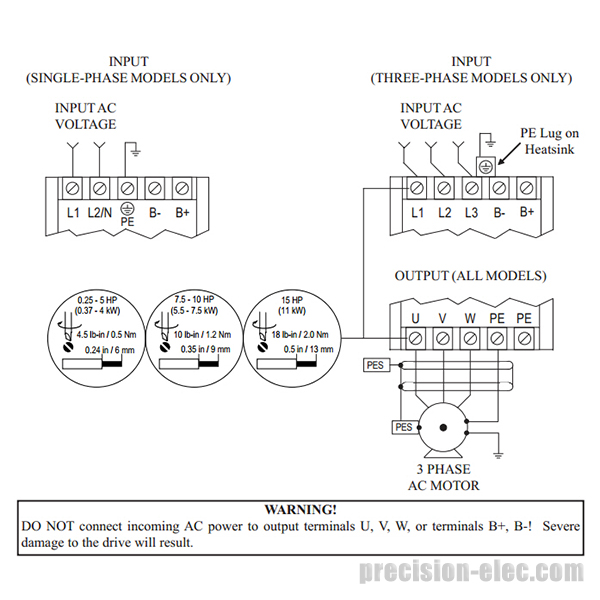
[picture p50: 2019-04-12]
00 - R7 Documentation/R7 VFD Inverter Wiring/VFD Motor Wiring.jpg

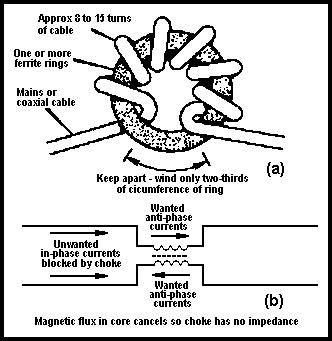
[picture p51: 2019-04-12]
00 - R7 Documentation/R7 VFD Inverter Wiring/Ferrite Ring wiring.jpg

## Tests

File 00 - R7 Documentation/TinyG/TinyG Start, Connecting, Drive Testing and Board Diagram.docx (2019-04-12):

# TinyG Start, Connecting, Drive Testing and Board Diagram

Frode Lillerud edited this page on Jan 9 · 108 revisions (https://github.com/synthetos/TinyG/wiki/TinyG-Start/_history)

(copied from Synthetos github; https://github.com/synthetos/TinyG/wiki/TinyG-Start)

If you have a TinyG v8 this is the place to start. The board revision is printed on the silkscreen at the edge of the board. If you do not have a v8 board you may want one of these links instead:

- TinyG version 7 (https://github.com/synthetos/TinyG/wiki/TinyG-Start-v7/)
- TinyG version 6 or earlier (https://github.com/synthetos/TinyG/wiki/TinyG-Start-v6-and-Earlier)

Here's some background if you want to know about TinyG (https://github.com/synthetos/TinyG/wiki/What-is-TinyG)
Here's some additional information about Initial Setup (https://github.com/synthetos/TinyG/wiki/Initial-Setup)
Here is a list of differences between the v7 and v8 boards (https://github.com/synthetos/TinyG/wiki/TinyG-Start)

Here are the steps to get started. We recommend following them in order.

- What You Need (https://github.com/synthetos/TinyG/wiki/TinyG-Start) (TinyG board, motors, power supply, fan (optional))
- Connecting TinyG (https://github.com/synthetos/TinyG/wiki/connecting-tinyG)
- Setting Up Your Machine and Configuring TinyG (https://github.com/synthetos/TinyG/wiki/tinyg-configuration)
  - About your CNC
    - Shapeoko2 section
  - Configuring motors
  - Configuring axes
  - Configuring system and communication parameters

## Read This First

The getting started page is your first place to go to figure out what you need to get to get your TinyG up and running quickly. However before we dive into hooking up wires, configuring, and running Gcode files the image below is a "diagram" of the important sections / parts of your TinyG board.

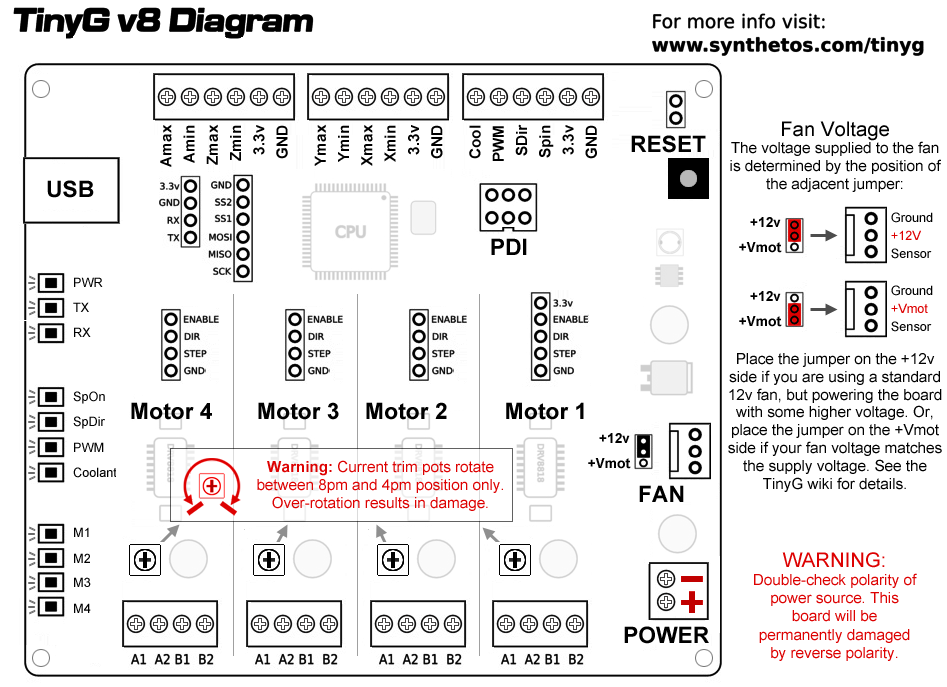
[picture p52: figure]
TinyG diagram version 8

To highlight a few things in the above diagram:

- The MOST IMPORTANT thing to do is to wire your power input correctly. The input will take up to 30 volts, but most people use 24, 19 or 12 volt power supplies. Double check that the polarity for the GND and Vmot are correct BEFORE plugging in your TinyG board. If you have ANY doubt about the power supply output please check it with a volt meter first.
- Power output for the PC fan is important to make sure you have right! Failure to set your fan jumper may result in providing 24v to a 12v fan and maybe blowing it up. See more about this below.
- All logic input voltages are limited to 3.3v MAX!
- Start with the current setting trim pots in the middle, 6:00, straight-up-and-down position. These are single-turn trim pots that travel about 270 degrees. DO NOT over torque the trim pots!

### What You Need

Here is what you are going to need in order to use TinyG:

- TinyG board (http://synthetos.myshopify.com/products/tinyg)
- Stepper motors (https://github.com/synthetos/TinyG/wiki/TinyG-Start)
- Power supply (https://github.com/synthetos/TinyG/wiki/TinyG-Start)

Optional

- Fan - A 12VDC or 24VDC fan is recommended if the motors are pulling more than 2 amps per winding, especially if the board is in an enclosure.
- Programmer/Debugger You can use TinyG's Bootloader (https://github.com/synthetos/TinyG/wiki/TinyG-Boot-Loader) for firmware updates, so you don;t need a programmer. But if you want to do real-time debugging or serious development we recommend picking up a programmer.

### TinyG Board

You can get the TinyG controller board fully assembled from the Synthetos Store (https://synthetos.myshopify.com/products/tinyg). Details of the board are in the diagram at the beginning of this page.

### Stepper Motors

The next thing you chose (or are chosen by your machine) are the stepper motors. TinyG will work with most NEMA17 and NEMA23 motors, and will work with both bipolar and unipolar stepper motors. This covers most small motors you are likely to encounter. It will not work with motors wired as 5 wire "star configurations", so avoid these.

We have never found a NEMA17 that would not work with TinyG, and almost every NEMA23 we have tried will work if rated up to about 3 amps per winding. The drivers on the TinyG v8 are rated to 2.5A per winding per motor, but will actually do up to 3 amps with proper cooling. Almost every NEMA17 motor we have seen draws less than 2 amps. The exceptions are some of those very long NEMA17s with torque ratings above 90 Oz-in. Most NEMA 23's we are familiar with are between 2 and 3 amps (and should therefore be fan cooled).

We also routinely run NEMA34's, but not in high mechanical load situations. The motor's rated voltage is irrelevant and can be ignored. When running NEMA23's or any motor that draws more than 2 amps we recommend fan cooling. Note that most of the heat comes off the bottom copper, so be sure to provide air circulation for the bottom of the board as well as the top.

Some of out favorite sources for stepper motors are:

- Automation Technology Inc. (Keling) (http://www.automationtechnologiesinc.com/)
- Alltronics (http://www.alltronics.com/cgi-bin/category/55%20www.alltronics.com/cgi-bin/category/55)
- MPJA (http://www.mpja.com/Stepper-Motors/products/101/%20www.mpja.com/Stepper-Motors/products/101/)
- [All Electronics](http://www.allelectronics.com/make-a-store/category/400/Motors/1.html
- Sparkfun (https://www.sparkfun.com/categories/178)
- Phidgets (http://www.phidgets.com/products.php?category=23)
- Oriental Motor Company (http://www.omc-stepperonline.com/)

### Power Supply

We highly recommend a 24v-30v power supply. While 12 volt operation is possible and entirely fine, running with a 24v power supply will allow the motors to be more responsive and actually run cooler (ironically).

You might think that 4 motors at 2 amps per winding would require 4 motors * 2 windings * 2 amps = 16 amps to drive, but you'd be wrong. 4 to 4.5 amps or above will handle this as not all motors + phases are ever maxed out at the same time. At 24 volts we like to have at least 4.5 amps for NEMA17's and 6 or more is recommended for NEMA23s.

Here are a couple power supplies we like:

- Meanwell NES-150-24 (http://www.mouser.com/ProductDetail/Mean-Well/NES150-24/)
- Meanwell NES-350-24 (http://www.mouser.com/ProductDetail/Mean-Well/NES-350-24/)

You can usually hunt around and find them for < $50. They also make lower amperage supplies that are cheaper.

PS Caveat: Be sure to switch the AC input from 240v to 120v if you are in the US or a 120v mains country. Most PSs will still work, but will audibly "click" and lose power if you don't set this correctly. Also, we've gotten Meanwell clones ordering from eBay - like Meigwei. Sheesh - they said I was ordering a Meanwell.

### Cooling

The main heatsinking provided for TinyG is the expanse of 2 oz. copper on the bottom and top of the board. You can see this by inspection. This is usually sufficient for NEMA17 installations and many NEMA23 applications. If you experience thermal shutdown or if you feel the chips are running too hot we recommend fan cooling.

The TI drivers on the TinyG are incredibly robust and will shut down in case of over-current instead of blowing up (unlike some other brands that shall remain nameless). But you don't want to go into thermal shutdown as it will will ruin your job even though the board is still OK. Thermal shutdown is evidenced by anything from a slow on-off cycling of the motor power, getting shorter as the current raises, to a stutter in extreme cases. The chips will be quite hot to the touch.

Fan cooling is the most effective way to cool and far more effective than heatsinking. Just putting little heatsinks on the top doesn't do much good. We used to sell TinyG with these but don't any more.

The TinyGv8's come equipped with a 3-pin fan connector that can be used to power a standard 12vdc PC fan, or a 24vdc fan - depending on a jumper setting and your board voltage (Vmot). Please read the silkscreen designators as below:

- The +12v jumper position connects the fan header to the on-board 12 volt regulator. This should be used if you are running a 12 volt fan and your board power (Vmot) is greater than 14 volts. This is the default jumper position and your v8 should have been shipped with the jumper in this position.
- The +Vmot jumper position connects the fan header directly to the board power (Vmot). In this case your fan voltage needs to be the same as your motor voltage, be it 12 volts, 24 volts, or anything else. Use this side with caution as applying 24 volts to some 12 volt fans will burn them out.

### Programmer/Debugger

If you are doing serious development or want to do real-time debugging we recommend getting a programmer debugger. The unit of choice these days is the ATMEL-ICE-BASIC programmer (http://www.digikey.com/product-detail/en/ATATMEL-ICE-BASIC/ATATMEL-ICE-BASIC-ND/4753381). The BASIC sells for about $50 and will program and debug AVRs (like the Xmega on the TinyG v8) as well as the Atmel ARM chip on the pre-release TinyG v9. Note that as of now AVRdude will not program using the ATMEL-ICE. In addition to multi-chip programming, the Atmel-ICE offers real-time debugging via Atmel Studio or Open OCD.

The older Atmel AVRISP MKII programmer (http://www.mouser.com/Search/ProductDetail.aspx) will also program the Xmega, and does work with AVRdude. But it doesn't do debugging and won't work with the ARM chips.

Note that older AVR ICSP programmers will not work.

### Connecting TinyG

At this point you can move on to Connecting TinyG (https://github.com/synthetos/TinyG/wiki/Connecting-TinyG)

# Changes in v8 from v7

- LEDs moved to a single edge for better mounting / readout
- USB changed to USB-B (from mini) for better mechanical integrity
- IO connections changed from 0.100 headers to screw terminal blocks
- step/direction/enable signals broken out on headers for external stepper drivers
- logic power supply is now a switcher (as opposed to a linear) on the v7 for better thermal characteristics
- FTDI USB chip changed to FT230X from FT232R
- switch inputs have RC circuit built in for better noise rejection
- RS-485 removed and replaced with SPI connection
- transient voltage suppressors added to Vmotor and USB lines
- mounting hole pattern is slightly different to accommodate about 1/4" growth in the board

# Connecting TinyG

Alden Hart edited this page on Aug 6 · 94 revisions (https://github.com/synthetos/TinyG/wiki/Connecting-TinyG/_history)

If you are on this page you have already selected your motors and power supply and are ready to hook them up.

Connecting TinyG Steps

- Connect power (https://github.com/synthetos/TinyG/wiki/Connecting-TinyG)
- Connect USB (https://github.com/synthetos/TinyG/wiki/Connecting-TinyG)
- Test connection (https://github.com/synthetos/TinyG/wiki/Connecting-TinyG)
- Wire your motors (https://github.com/synthetos/TinyG/wiki/Connecting-TinyG)
- Set motor current (https://github.com/synthetos/TinyG/wiki/Connecting-TinyG)
- Test drive (https://github.com/synthetos/TinyG/wiki/Test-Drive-TinyG)

## Connect Power

The MOST IMPORTANT thing to do is to wire your power input correctly. So check and double check this before actually turning on the power.

THIS PAGE ASSUMES THAT THE POWER SUPPLY'S BLACK IS GROUND AND RED OR YELLOW IS +24VOLT (HOT). Not all power supplies adhere to this convention so you still need to check this carefully. Read below:

1. Check you have the correct power supply. You should have a DC power supply between 12 and 30 volts --- 24 volts is ideal. It should be capable of providing 4 to 15 amps.
2. If you have a power supply where you are responsible for wiring the AC lines (like a Meanwell or some other supply with a terminal strip) - make sure the AC is wired correctly. By convention, the AC neutral is the white wire in the power cord, the hot is the black wire and the ground is green. Make sure the ground is connected. Not only for safety, but also because you may experience spurious resets if the system is not properly grounded.
3. BEFORE connecting it to TinyG, turn on the power supply and make sure you have correct voltage. Make sure it is DC, not AC. Hopefully you have a volt meter or can get your hands on one. If you don't you might consider a trip to the Radar Shed for something like this one from Sparkfun (https://www.sparkfun.com/products/12966) or this one from Adafruit (http://www.adafruit.com/products/2034).
4. With the power supply off, wire the negative to the GND terminal of the power input block, and the positive to the +Vmot side. Negative is BLACK by convention and positive is RED or YELLOW, or some other bright color. Check you have the correct voltage and polarity before connecting the power supply to TinyG. We have encountered power supplies that do not obey these conventions, and incorrect voltage or polarity can destroy your board!
5. Turn on the power supply. If the blue light turns on this is a good sign. If not, blow away the smoke and send us an email.

## Establish USB connection

Next establish USB connection with your host computer.

#### Install FTDI Drivers

- If you do not have the FTDI VCP USB drivers for your host computer you will need to install them. It's possible they are already on your system as many applications use them, including the older Arduinos.
- PC Installation - Get the latest Windows driver from the FDTI VCP Driver Page (http://www.ftdichip.com/Drivers/VCP.htm). You want the VCP driver for your host, not some of the other drivers they offer. Install and reboot your system.
- MAC Installation - As of Mavericks (OSX 10.9.x) OSX will appear to communicate with TinyG without loading the FTDI supplied drivers. However, the native mac drivers do not perform flow control with the FTDI on the v8, so they will not work. You need the VCP 2.3 driver from the FDTI VCP Driver Page (http://www.ftdichip.com/Drivers/VCP.htm). You must also reboot your system once the installation is finished (they don't tell you this). If installed correctly you should see something like usbserial-DA00Y5MM when you scan for new serial ports.

Note that the Mac native driver will also show the usbserial port, so the only real way to tell if you have the FTDI driver is to look in APPLE_IN_THE_UPPER_LEFT_CORNER / About This Mac / System Report / Software / Extensions for FTDIUSBSerialDriver, version 2.3)

#### Set up Coolterm

Once you have the FTDI drivers in place you will want Roger Meier's Coolterm to connect and test your tinyg. Coolterm is a terminal emulator that provides command line access to TinyG and can also stream files to TinyG. We use Coolterm as the preferred way to test the board without introducing variables from advanced UIs and host controllers such as ChiliPeppr (https://github.com/synthetos/TinyG/wiki/Chilipeppr), which is a better way to actually run jobs once you have the system set up.

- Download and install Coolterm (http://freeware.the-meiers.org/). For the Mac we have noticed that the latest version (1.4.5) does not do well on large file transmissions. So we still use version 1.4.3. This is available on the Coolterm page under Previous Releases (http://freeware.the-meiers.org/previous/).
- Go to the Options menu and Re-Scan Serial Ports. You should see something like usbserial-AE01DVWD or COM12. Configure the following settings:
  - 115,200 baud
  - 8 data bits
  - no parity
  - 1 stop bit
  - XON flow control (or use CTS, but make sure the $ex setting agrees)
- It's also useful to set the following - but not strictly necessary
  - Options/Terminal - Line Mode
  - Options/Enter Key Emulation - CR
- Hit OK to leave the Options menu

#### Test Connection to TinyG

- Hit the "Connect" button. Enter a few carriage returns. TinyG should respond with prompts. If not, hit the reset button on the TinyG. You should see some JSON startup messages wrapped in JSON curly braces something like this:
- {"r":{"fb":371.030,"fv":0.950,"hv":7.000,"id":"9H3583-RMP","msg":"Loading configs from EEPROM","f":[1,15,0,8891]}}
- {"r":{"fb":371.030,"fv":0.950,"hv":7.000,"id":"9H3583-RMP","msg":"SYSTEM READY","f":[1,0,0,8820]}}
- tinyg [mm] ok>
- If not, go back and check your driver, your serial settings, your USB cable, and that you have a blue light and not blue smoke. For help from the command line enter 'h' for TinyG help, or '$h' for configuration help
- If you simply cannot connect try powering down the TinyG and quitting Coolterm (or your terminal program), powering back up and restarting the terminal. There is a known bug in the FTDI drivers that can cause this sometimes.

Verify Flow Control Once you are connected it's a good idea to verify you have the correct flow control settings

- The default flow control for TinyG is CTS, which uses the following settings:
  - Coolterm: CTS checked
  - TinyG $ex=2
- XON/XOFF flow control is also available. Both Coolterm and TinyG must be configured the with these settings:
  - Coolterm: XON checked
  - TinyG: $ex=1

## Wire Your Motors

It's best to wire your motors when they are not yet in your machine. This way you can test drive them without worrying about mechanical issues such as excessive friction or crashing into the side of the machine.

If your motors are already in a machine sometimes it's easier just to use one or more spare motors rather than remove them. It will not damage the TinyG board to drive an axis with no motor attached.

But first, turn off the power to TinyG. Never connect or disconnect anything (except possibly USB) with the power on.

### Motor Connectors (was "Synthetos Connector Kit")

Most TinyG v7s and above have screw terminals and therefore do not need a motor connector kit. If you have a board that has quick release headers on it here are the mating parts:

- Terminal Shell - Molex 09-50-3041 (need 1 per motor)
- Crimp Terminals - Molex 08-50-0134 (need 4 per motor, and usually some extras)

You need 4 terminals for each housing (shell). You can get these from Mouser or DigiKey. TE/Amp also makes some nice parts with the shell and terminals all-in-one:

- TE/Amp 3-644463-4 (need one per motor)

### Find the Coil Pairs

The first step is make sure you know which wires are connected to the same coil.

The following are common motor types:

- Bipolar motors have 4 wires (2 pairs). This wire color code is typical for many bipolar motors:

Wire Color | Winding
Green | Winding A1
Black | Winding A2
Red | Winding B1
Blue | Winding B2

- Unipolar motors typically have 6 wires also connected to to 2 windings. The additional wires are the center taps for each winding. These can usually be ignore (not connected). This wire color code is typical for many unipolar motors:

Wire Color | Winding
Green | Winding A1
Yellow | Center tap A
Black | Winding A2
Red | Winding B1
White | Center tap B
Blue | Winding B2

- 8 wire motors: 8 wire motors are usually wired as 2 sets of bipolar windings - essentially these are 2 bipolars wired together. They can be wired by finding which pairs are in parallel with each other and either not using the second winding, or wiring it in parallel for more torque (and more current draw). There is no common color code for 8 wire motors. (Please correct me if I'm wrong).
- 5 wire motors are in a "star" configuration that has a common ground and require a specialized driver. TinyG cannot drive 5 wire steppers.

To determine which wires go to which windings use a volt meter to verify that green and black connect together, and red and blue connect together, and that they don't connect to the other pair. Typical DC resistance across a winding is about 1 to 5 ohms. If you have a Unipolar motor the center taps will show 1/2 the resistance of the full winding.

Here's a shortcut to finding wire pairs for a bipolar (4 wire) motor.

Spin your stepper motor with your fingers. Depending on the size / holding torque this could be easy or pretty hard. All you really want from this is to get a feel how the motor spins without any of the wires connected to each other. Now that you know how hard it is to spin with your fingers, connect 2 wires together. Just pick any two. Try to spin the motor again. If it feels the same then more than likely these are NOT connected to the same coil. Disconnect these wires. Connect one of the other wires to one of the first wire pairs you tried. Try to spin the motors again. This should be much harder. If so, you have found your wire pairs. Tape these 2 together (not wired but just taped to group them). Tape the remaining 2 wires together as well.

Unipolars are a bit more complicated, but not much. To do a series wiring find the outer taps of each coil. These are often color coded by convention (see below). Using a volt meter to find the resistance across the outer pair. The resistance between the center tap an an outer tap will be 1/2 the resistance between the outer taps.

Some useful information on wiring steppers can be found here: http://reprap.org/wiki/Stepper_motor

### Connector Pinouts

Back to connecting your TinyG. Each of the 4 motor outputs have a four pin terminal block wired as:

- A1
- A2
- B1
- B2

Attach one pair to A1/A2 and the other pair to B1/B2. If your motor spins the wrong way, you can swap A1 with A2 and vice versa. This can also be done in software by using the polarity setting, e.g. $1po=1 to invert.
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

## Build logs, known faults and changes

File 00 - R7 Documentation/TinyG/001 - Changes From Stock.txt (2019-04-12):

$1tr=8
$1po=1
$2tr=8
$2po=1
$3ma=1
$3tr=8
$3po=1
$4ma=2
$4tr=8
$4pm=1
$xvm=4000
$xtm=750
$xsn=0
$xsx=3
$xsv=400
$yvm=4000
$ytm=750
$ysn=0
$ysx=3
$ysv=400
$zvm=4000
$ztm=750
$zsn=0
$zsx=3
$zsv=400

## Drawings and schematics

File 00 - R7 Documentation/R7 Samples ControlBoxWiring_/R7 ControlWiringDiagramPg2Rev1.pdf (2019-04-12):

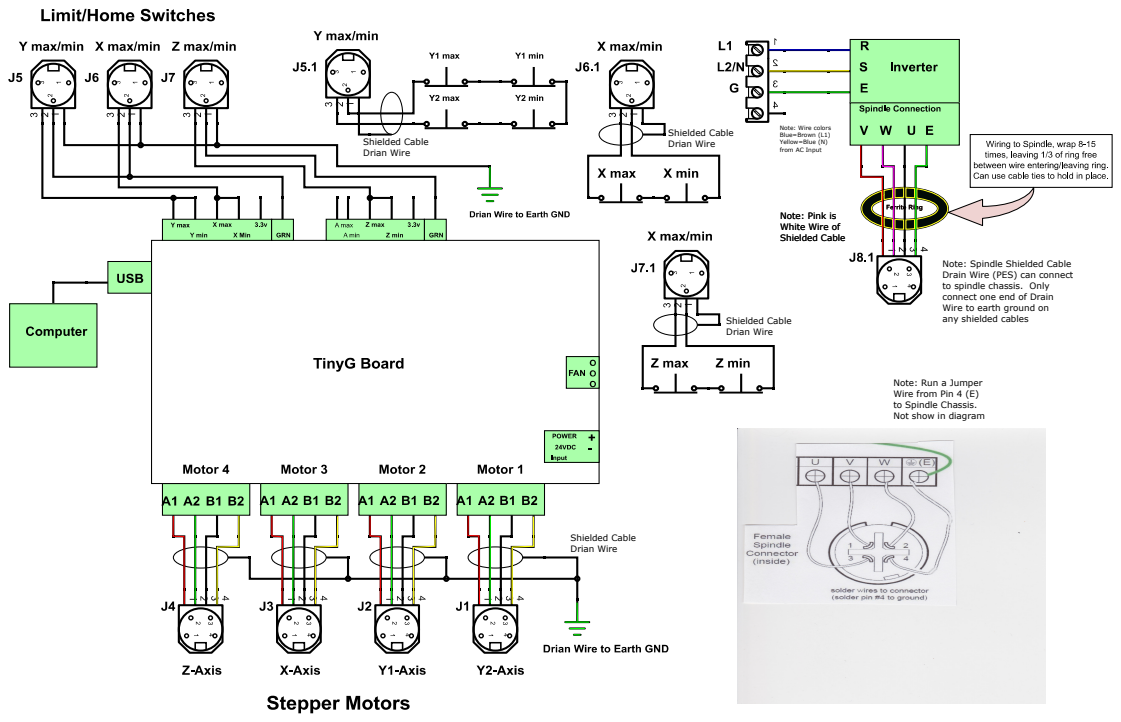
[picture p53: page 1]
Shielded Cable Drian Wire

Note: Wire colors
Blue=Brown (L1)
Yellow=Blue (N)
from AC Input

Note: Pink is
White Wire of
Shielded Cable

Note: Spindle Shielded Cable
Drain Wire (PES) can connect
to spindle chassis. Only
connect one end of Drain
Wire to earth ground on
any shielded cables

Note: Run a Jumper
Wire from Pin 4 (E)
to Spindle Chassis.
Not show in diagram

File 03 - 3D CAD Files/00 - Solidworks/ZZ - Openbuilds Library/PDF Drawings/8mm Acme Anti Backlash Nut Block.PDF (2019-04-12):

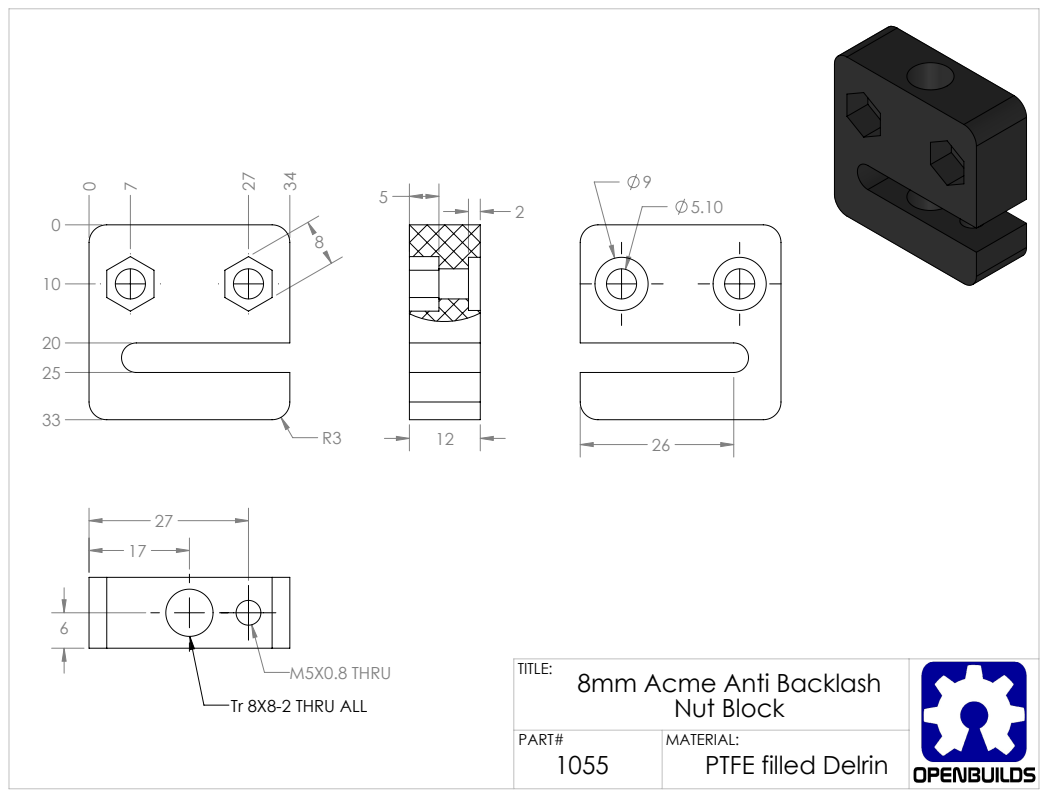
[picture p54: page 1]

M5X0.8 THRU
Tr 8X8-2 THRU ALL

TITLE: 8mm Acme Anti Backlash Nut Block

PART# 1055 | MATERIAL: PTFE filled Delrin

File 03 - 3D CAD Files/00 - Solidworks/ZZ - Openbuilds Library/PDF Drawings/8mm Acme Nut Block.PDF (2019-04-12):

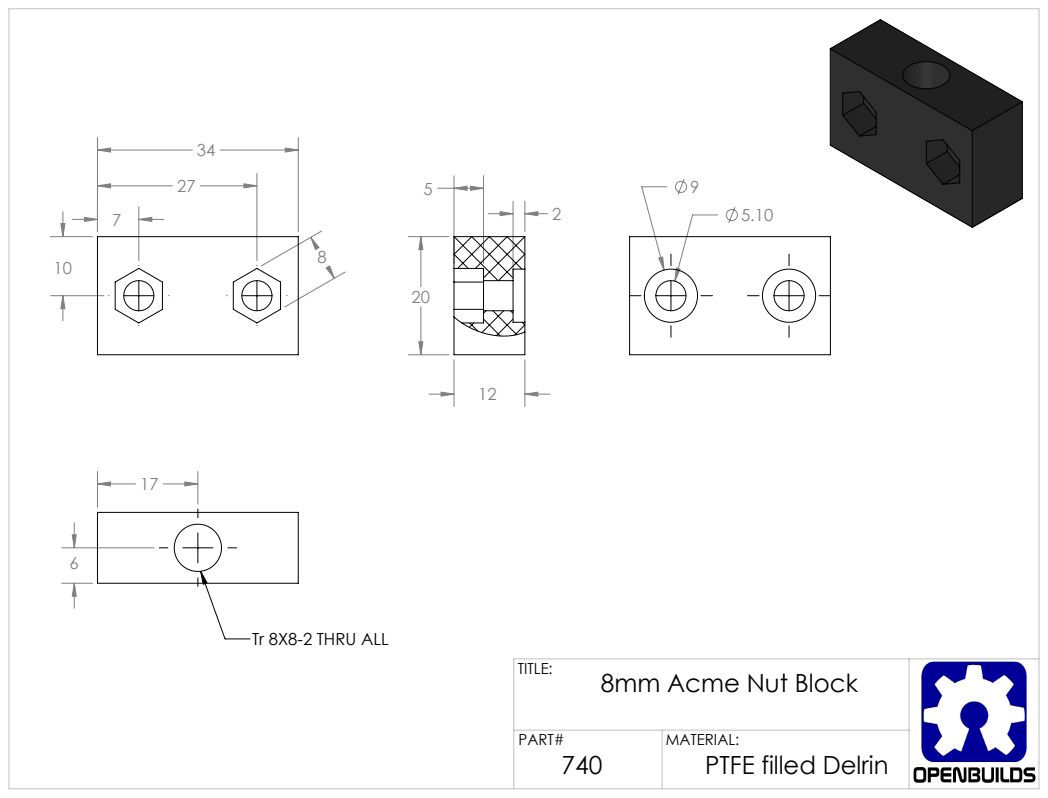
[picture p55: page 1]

Tr 8X8-2 THRU ALL

TITLE: 8mm Acme Nut Block

PART# 740 | MATERIAL: PTFE filled Delrin

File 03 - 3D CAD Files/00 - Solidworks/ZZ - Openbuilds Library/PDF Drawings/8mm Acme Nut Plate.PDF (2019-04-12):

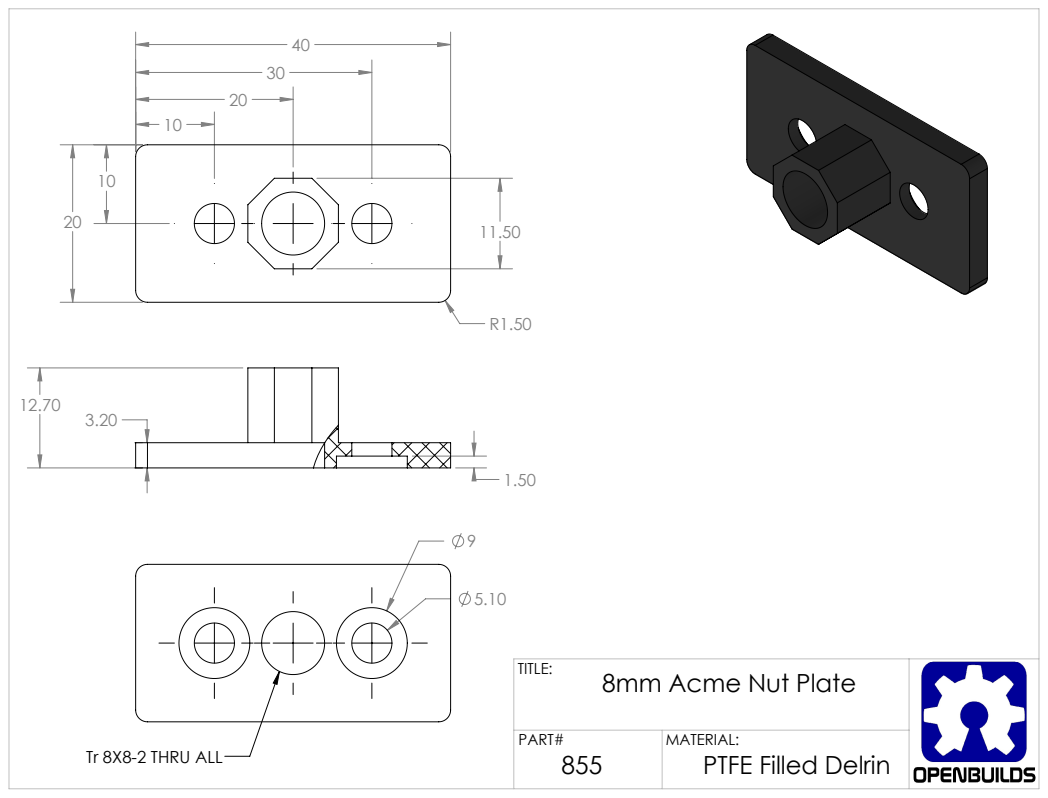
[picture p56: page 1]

TITLE: 8mm Acme Nut Plate

PART# 855 | MATERIAL: PTFE Filled Delrin

Tr 8X8-2 THRU ALL

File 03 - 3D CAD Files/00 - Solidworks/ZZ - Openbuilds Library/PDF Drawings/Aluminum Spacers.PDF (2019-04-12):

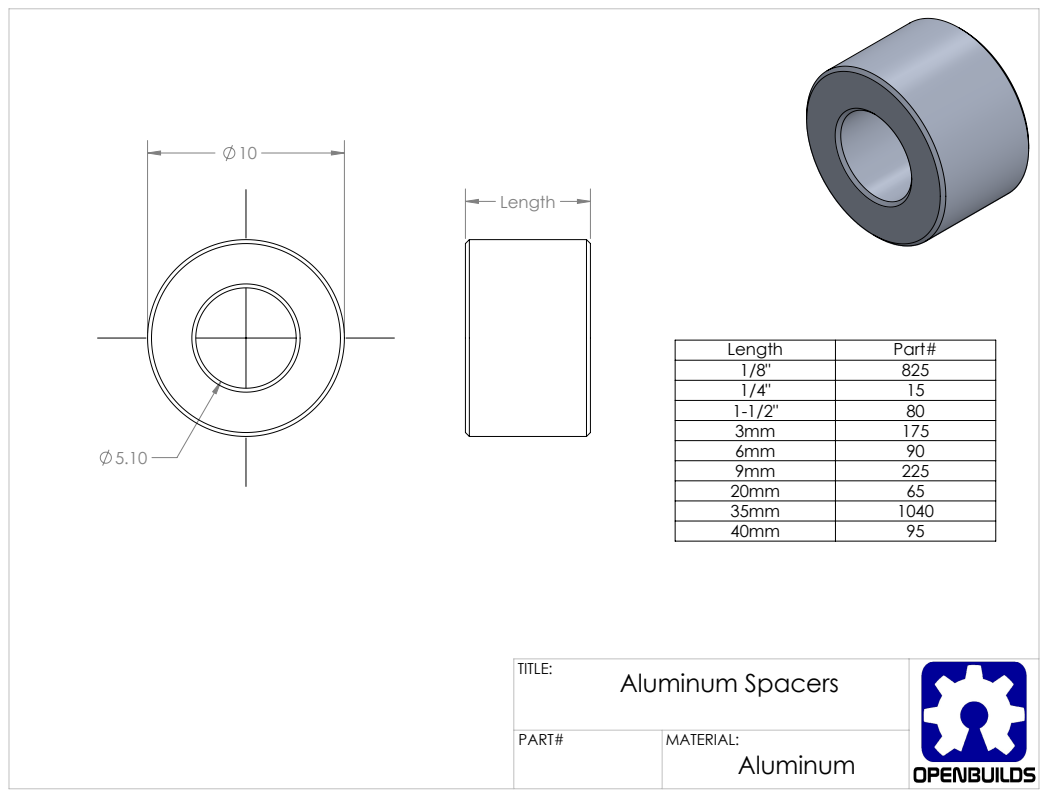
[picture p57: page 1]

Length | Part#
1/8" | 825
1/4" | 15
1-1/2" | 80
3mm | 175
6mm | 90
9mm | 225
20mm | 65
35mm | 1040
40mm | 95

TITLE: Aluminum Spacers

PART# | MATERIAL: Aluminum

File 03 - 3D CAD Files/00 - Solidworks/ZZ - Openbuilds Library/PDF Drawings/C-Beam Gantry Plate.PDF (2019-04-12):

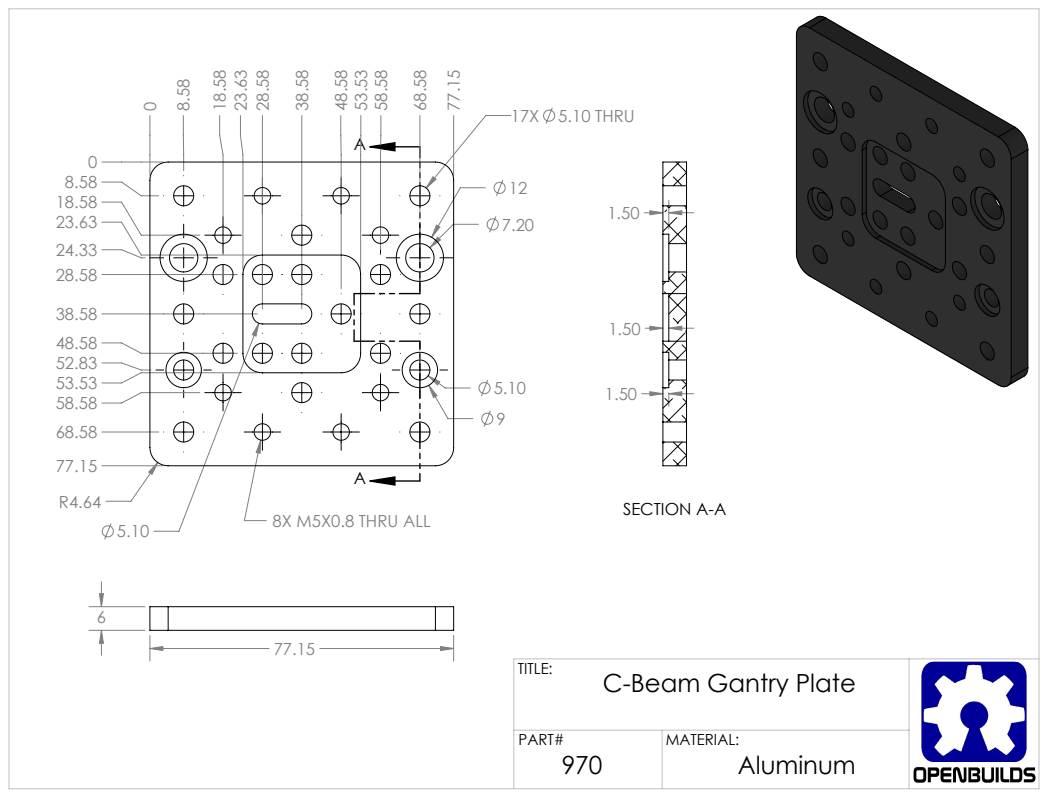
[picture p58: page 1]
8X M5X0.8 THRU ALL; 17X 5.10 THRU; SECTION A-A

TITLE: C-Beam Gantry Plate

PART# 970 | MATERIAL: Aluminum

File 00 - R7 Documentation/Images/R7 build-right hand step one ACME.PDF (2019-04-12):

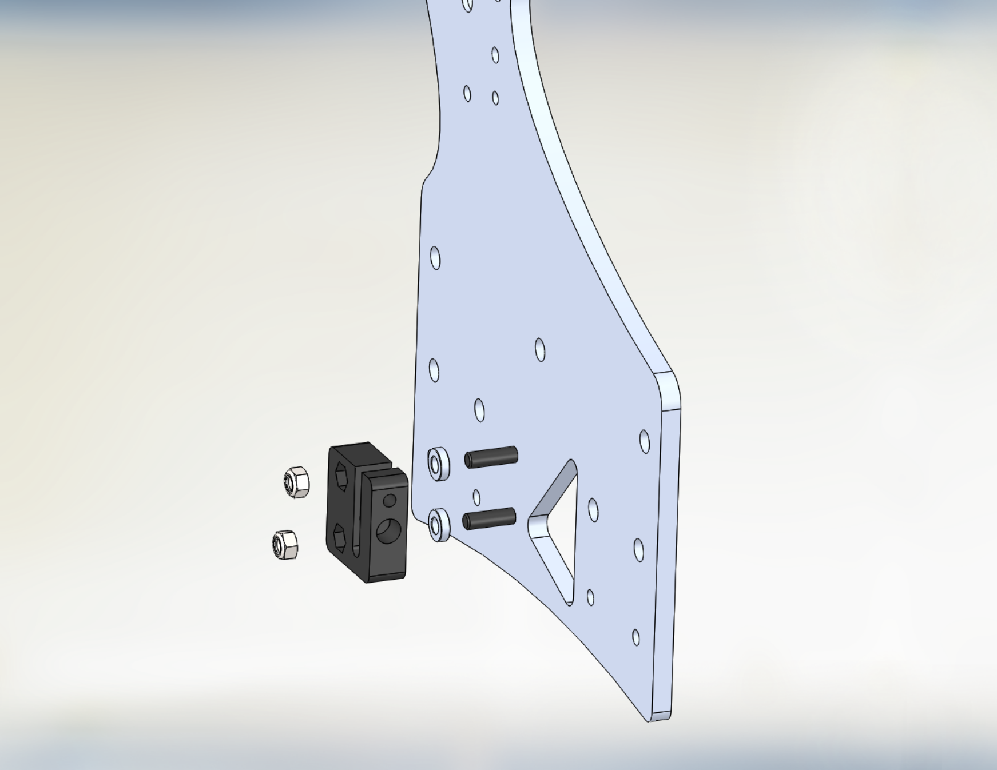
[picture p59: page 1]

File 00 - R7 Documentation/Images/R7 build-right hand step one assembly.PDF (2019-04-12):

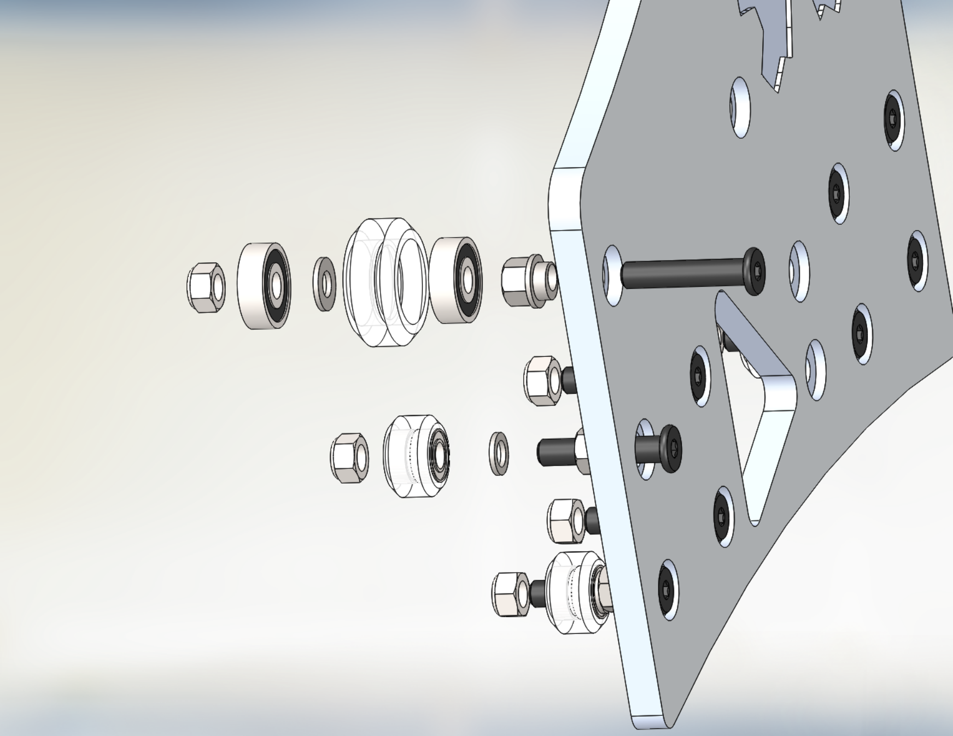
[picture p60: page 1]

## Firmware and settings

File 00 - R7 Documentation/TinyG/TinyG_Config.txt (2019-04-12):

 $$
 {"ej":""}
[fb]  firmware build            440.18
[fv]  firmware version            0.97
[hp]  hardware platform           1.00
[hv]  hardware version            8.00
[id]  TinyG ID                    2U2971-ZHS
[ja]  junction acceleration  100000 mm
[ct]  chordal tolerance           0.0100 mm
[sl]  soft limit enable           0
[st]  switch type                 0 [0=NO,1=NC]
[mt]  motor idle timeout          0.10 Sec
[ej]  enable json mode            0 [0=text,1=JSON]
[jv]  json verbosity              1 [0=silent,1=footer,2=messages,3=configs,4=linenum,5=verbose]
[js]  json serialize style        1 [0=relaxed,1=strict]
[tv]  text verbosity              1 [0=silent,1=verbose]
[qv]  queue report verbosity      1 [0=off,1=single,2=triple]
[sv]  status report verbosity     1 [0=off,1=filtered,2=verbose]
[si]  status interval           250 ms
[ec]  expand LF to CRLF on TX     0 [0=off,1=on]
[ee]  enable echo                 0 [0=off,1=on]
[ex]  enable flow control         1 [0=off,1=XON/XOFF, 2=RTS/CTS]
[baud] USB baud rate              5 [1=9600,2=19200,3=38400,4=57600,5=115200,6=230400]
[net] network mode                0 [0=master]
[gpl] default gcode plane         0 [0=G17,1=G18,2=G19]
[gun] default gcode units mode    1 [0=G20,1=G21]
[gco] default gcode coord system  1 [1-6 (G54-G59)]
[gpa] default gcode path control  2 [0=G61,1=G61.1,2=G64]
[gdi] default gcode distance mode 0 [0=G90,1=G91]
[1ma] m1 map to axis              0 [0=X,1=Y,2=Z...]
[1sa] m1 step angle               1.800 deg
[1tr] m1 travel per revolution    1.2500 mm
[1mi] m1 microsteps               8 [1,2,4,8]
[1po] m1 polarity                 0 [0=normal,1=reverse]
[1pm] m1 power management         2 [0=disabled,1=always on,2=in cycle,3=when moving]
[2ma] m2 map to axis              1 [0=X,1=Y,2=Z...]
[2sa] m2 step angle               1.800 deg
[2tr] m2 travel per revolution    1.2500 mm
[2mi] m2 microsteps               8 [1,2,4,8]
[2po] m2 polarity                 0 [0=normal,1=reverse]
[2pm] m2 power management         2 [0=disabled,1=always on,2=in cycle,3=when moving]
[3ma] m3 map to axis              2 [0=X,1=Y,2=Z...]
[3sa] m3 step angle               1.800 deg
[3tr] m3 travel per revolution    1.2500 mm
[3mi] m3 microsteps               8 [1,2,4,8]
[3po] m3 polarity                 0 [0=normal,1=reverse]
[3pm] m3 power management         2 [0=disabled,1=always on,2=in cycle,3=when moving]
[4ma] m4 map to axis              3 [0=X,1=Y,2=Z...]
[4sa] m4 step angle               1.800 deg
[4tr] m4 travel per revolution  360.0000 mm
[4mi] m4 microsteps               8 [1,2,4,8]
[4po] m4 polarity                 0 [0=normal,1=reverse]
[4pm] m4 power management         2 [0=disabled,1=always on,2=in cycle,3=when moving]
[xam] x axis mode                 1 [standard]
[xvm] x velocity maximum        800 mm/min
[xfr] x feedrate maximum        800 mm/min
[xtn] x travel minimum            0.000 mm
[xtm] x travel maximum          150.000 mm
[xjm] x jerk maximum             20 mm/min^3 * 1 million
[xjh] x jerk homing              40 mm/min^3 * 1 million
[xjd] x junction deviation        0.0500 mm (larger is faster)
[xsn] x switch min                1 [0=off,1=homing,2=limit,3=limit+homing]
[xsx] x switch max                0 [0=off,1=homing,2=limit,3=limit+homing]
[xsv] x search velocity         500 mm/min
[xlv] x latch velocity          100 mm/min
[xlb] x latch backoff             5.000 mm
[xzb] x zero backoff              1.000 mm
[yam] y axis mode                 1 [standard]
[yvm] y velocity maximum        800 mm/min
[yfr] y feedrate maximum        800 mm/min
[ytn] y travel minimum            0.000 mm
[ytm] y travel maximum          150.000 mm
[yjm] y jerk maximum             20 mm/min^3 * 1 million
[yjh] y jerk homing              40 mm/min^3 * 1 million
[yjd] y junction deviation        0.0500 mm (larger is faster)
[ysn] y switch min                1 [0=off,1=homing,2=limit,3=limit+homing]
[ysx] y switch max                0 [0=off,1=homing,2=limit,3=limit+homing]
[ysv] y search velocity         500 mm/min
[ylv] y latch velocity          100 mm/min
[ylb] y latch backoff             5.000 mm
[yzb] y zero backoff              1.000 mm
[zam] z axis mode                 1 [standard]
[zvm] z velocity maximum        800 mm/min
[zfr] z feedrate maximum        800 mm/min
[ztn] z travel minimum            0.000 mm
[ztm] z travel maximum           75.000 mm
[zjm] z jerk maximum             20 mm/min^3 * 1 million
[zjh] z jerk homing              40 mm/min^3 * 1 million
[zjd] z junction deviation        0.0500 mm (larger is faster)
[zsn] z switch min                0 [0=off,1=homing,2=limit,3=limit+homing]
[zsx] z switch max                1 [0=off,1=homing,2=limit,3=limit+homing]
[zsv] z search velocity         400 mm/min
[zlv] z latch velocity          100 mm/min
[zlb] z latch backoff             5.000 mm
[zzb] z zero backoff              1.000 mm
[aam] a axis mode                 3 [radius]
[avm] a velocity maximum     230400 deg/min
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

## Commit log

2019-04-12 Initial Upload
    Initial Upload
    [110 AC inlet.SLDPRT, 120 Angle Tee Nut.SLDPRT, 135 Angle Tee Nut.SLDPRT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]
2019-04-14 Add spreadsheets copied from google sheets
    [BOM.ods, Erics Speed and Feed Cheat Sheet.xlsx (1).ods, Erics Speed and Feed Cheat Sheet.xlsx (2).ods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]
2019-04-15 Outdated DXF removal
    Outdated DXF removal
    [R7 Complete set.dxf]
2019-04-15 Outdated DXF removal2
    Outdated DXF removal2
    [R7 Complete set w limits.dxf]
2019-04-15 Update DXF with feature type by layer
    Update DXF with feature type by layer:
    Profile
    Through Hole
    Counterbore
    Pocket
    Engrave
    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
    [R7-CNC_Plates.DXF]
2019-05-13 Grbl and Raspberry Pi files from Hobbyfab
    Here are the Grbl and Raspberry Pi (bCNC) files for the production HobbyFab Ox and R7 CNC machines. These were graciously provided by Brandon to help others trying to replicate the setup they provide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
2019-05-13 added Ox Grbl Readme
    Readme to help others find the right Grble File
2019-05-13 Create Readme for R7 Grbl
    Help users find the right Grbl files for the R7 CNC based on Spindle Size
2022-03-01 Add Dust Boot Fusion360 and Step Files
    Add Dust Boot Fusion360 and Step Files from Colin Kaminski
    [R7 Dust Boot v1.f3d, R7 Dust Boot v1.step]
